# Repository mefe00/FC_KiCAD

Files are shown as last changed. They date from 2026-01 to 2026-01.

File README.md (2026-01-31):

# FC_KiCAD
Projede STM32F405RGT6 MCU, ICM-42688-P IMU, BMP388 basınç sensörü ve istenirse harici takılabilmesi için SPI çıkışı ve I2C çıkışı mevcuttur. Projenin yazılımı github hesabım üzerinde mevcuttur ve geliştirilme aşamasındadır.

fc
cfff

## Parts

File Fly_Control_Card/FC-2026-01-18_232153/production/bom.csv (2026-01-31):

Designator | Footprint | Quantity | Value | LCSC Part #
C13, C21, C25, C28, C29 | 0603 | 5 | 100nF
C14, C16 | 0603 | 2 | 4.7uF/50V
C15 | 0603 | 1 | 0.1uF/50V
C17 | 0603 | 1 | 82pF/16V
C18, C19 | 0603 | 2 | 22uF/16V
C2, C3, C37, C4, C5, C9 | 0402 | 6 | 100nF
C20 | 0603 | 1 | 0.1uF/16V
C22, C24, C26, C27 | 0402 | 4 | 1uF
C23 | 0603 | 1 | 10nF/16V
C30, C31 | 0402 | 2 | 20pF
C40, C41, C7 | 0402 | 3 | 2.2uF
C6, C8 | 0402 | 2 | 0.1uF
D2 | D_SMA | 1 | SMAJ33A
D3 | D_SMC | 1 | D
D4 | 0603 | 1 | RED_LED
D5 | 0603 | 1 | BLUE_LED
D6 | 0603 | 1 | GREEN_LED
J1 | JST_SH_SM05B-SRSS-TB_1x05-1MP_P1.00mm_Horizontal | 1 | Conn_01x05_Socket
J2, J4, J5 | JST_SH_SM04B-SRSS-TB_1x04-1MP_P1.00mm_Horizontal | 3 | Conn_01x04_Socket
J6 | SolderWire-0.1sqmm_1x02_P3.6mm_D0.4mm_OD1mm | 1 | Conn_01x02_Pin
J7 | USB_C_Receptacle_GCT_USB4105-xx-A_16P_TopMnt_Horizontal | 1 | USB_C_Receptacle_USB2.0_16P
J8 | JST_SH_SM08B-SRSS-TB_1x08-1MP_P1.00mm_Horizontal | 1 | Conn_01x08_Socket
J9 | JST_SH_SM06B-SRSS-TB_1x06-1MP_P1.00mm_Horizontal | 1 | Conn_01x06_Socket
L1 | L_APV_ANR4026 | 1 | 10uH
R1, R2 | 0402 | 2 | 5.1k
R10 | 0603 | 1 | 3.16k
R11, R4 | 0402 | 2 | 330R
R12 | 0603 | 1 | 100k
R13 | 0402 | 1 | 1k
R14, R8 | 0402 | 2 | 4.7k
R15, R7 | 0402 | 2 | 10k
R16 | 0805 | 1 | 30k (28.18k)
R17 | 0805 | 1 | 10k
R18 | 0402 | 1 | 0
R19 | 0805 | 1 | 1k
R3 | 0402 | 1 | 100k
R5, R6 | 0402 | 2 | 22R
R9 | 0603 | 1 | 10k
SW1 | SW_Push_1P1T_NO_CK_KMR2 | 1 | SW_Push
U1 | LQFP-64_10x10mm_P0.5mm | 1 | STM32F405RGTx
U2 | SOT-23-6 | 1 | USBLC6-2SC6
U3 | SOT-23-5 | 1 | LP5907MFX-3.3
U5 | PQFN50P300X250X97-14N | 1 | ICM-42688-P
U6 | PQFN50P200X200X80-10N | 1 | BMP388
U7 | SOIC127P600X175-9N | 1 | RT8279GSP
U9 | SOT-23-5 | 1 | AP2112K-3.3
Y1 | Crystal_SMD_5032-2Pin_5.0x3.2mm | 1 | 8MHz

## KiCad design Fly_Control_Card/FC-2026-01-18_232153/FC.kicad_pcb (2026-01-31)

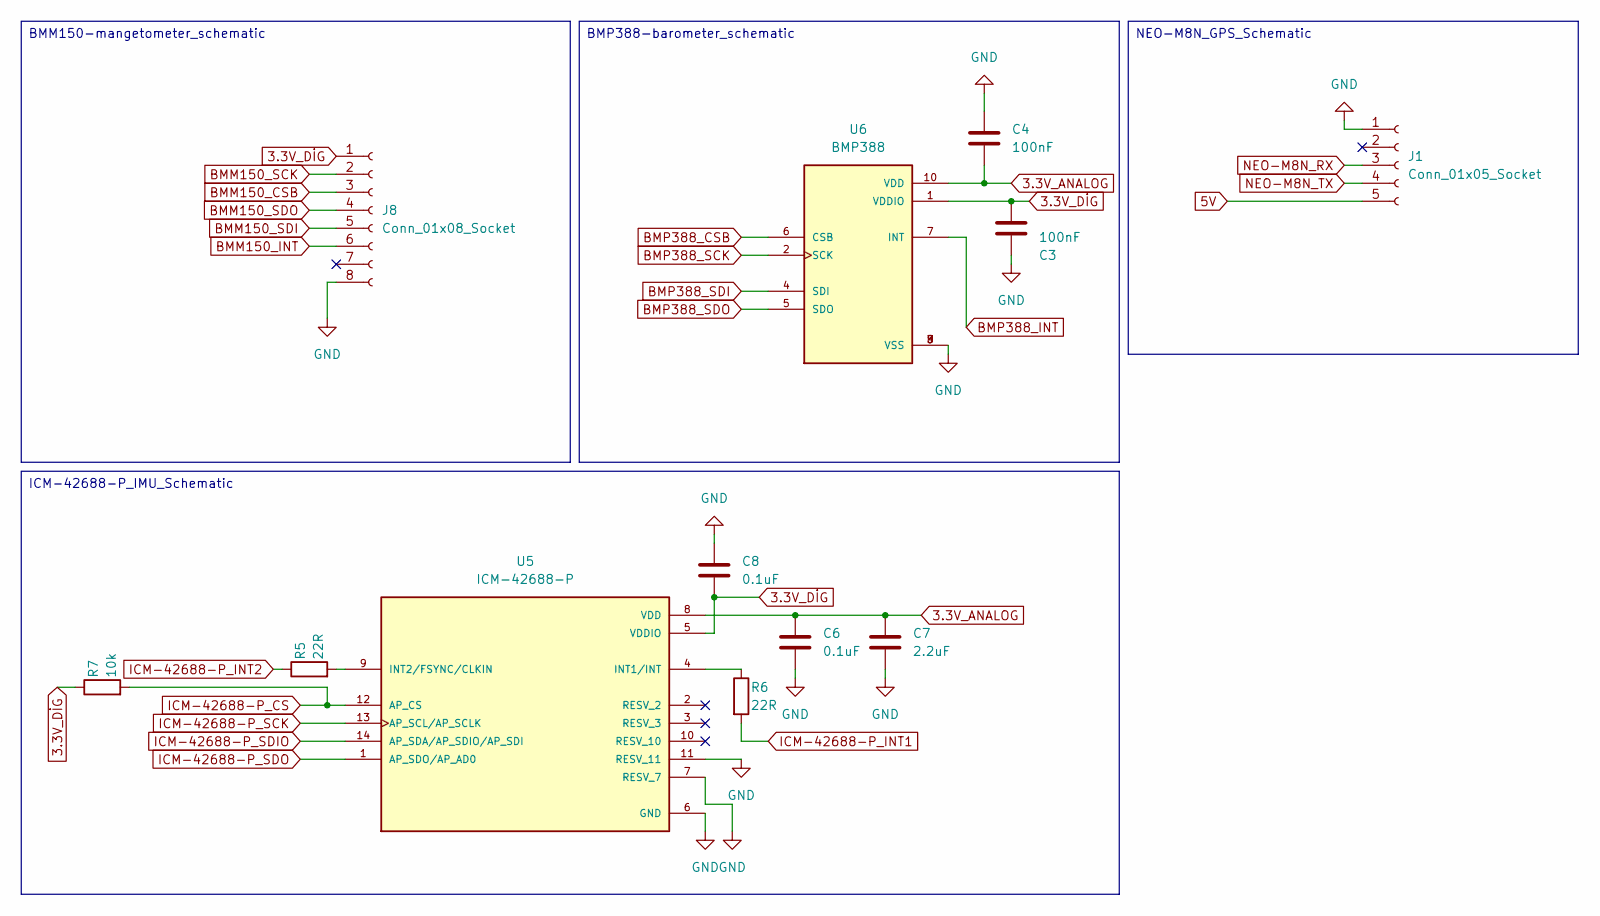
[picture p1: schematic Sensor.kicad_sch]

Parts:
C3, C4: 100nF; C_0402_1005Metric
C6, C8: 0.1uF; C_0402_1005Metric
C7: 2.2uF; C_0402_1005Metric
J1: Conn_01x05_Socket; JST_SH_SM05B-SRSS-TB_1x05-1MP_P1.00mm_Horizontal
J8: Conn_01x08_Socket; JST_SH_SM08B-SRSS-TB_1x08-1MP_P1.00mm_Horizontal
R5, R6: 22R; R_0402_1005Metric
R7: 10k; R_0402_1005Metric
U5: ICM-42688-P; PQFN50P300X250X97-14N; PARTREV 1.2
U6: BMP388; PQFN50P200X200X80-10N; PARTREV 1.1

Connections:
3.3V_ANALOG: C4.2, C6.1, C7.1, U5.8 (VDD), U6.10 (VDD); also elsewhere on the board
3.3V_DİG: C3.1, C8.2, J8.1, R7.1, U5.5 (VDDIO), U6.1 (VDDIO); also elsewhere on the board
5V: J1.5; also elsewhere on the board
BMM150_CSB: J8.3; also elsewhere on the board
BMM150_INT: J8.6; also elsewhere on the board
BMM150_SCK: J8.2; also elsewhere on the board
BMM150_SDI: J8.5; also elsewhere on the board
BMM150_SDO: J8.4; also elsewhere on the board
BMP388_CSB: U6.6 (CSB); also elsewhere on the board
BMP388_INT: U6.7 (INT); also elsewhere on the board
BMP388_SCK: U6.2 (SCK); also elsewhere on the board
BMP388_SDI: U6.4 (SDI); also elsewhere on the board
BMP388_SDO: U6.5 (SDO); also elsewhere on the board
GND: C3.2, C4.1, C6.2, C7.2, C8.1, J1.1, J8.8, U5.6 (GND), U5.7 (RESV_7), U5.11 (RESV_11), U6.3 (VSS), U6.8 (VSS), U6.9 (VSS); also elsewhere on the board
ICM-42688-P_CS: R7.2, U5.12 (AP_CS); also elsewhere on the board
ICM-42688-P_INT1: R6.2; also elsewhere on the board
ICM-42688-P_INT2: R5.1; also elsewhere on the board
ICM-42688-P_SCK: U5.13 (AP_SCL/AP_SCLK); also elsewhere on the board
ICM-42688-P_SDIO: U5.14 (AP_SDA/AP_SDIO/AP_SDI); also elsewhere on the board
ICM-42688-P_SDO: U5.1 (AP_SDO/AP_AD0); also elsewhere on the board
NEO-M8N_RX: J1.3; also elsewhere on the board
NEO-M8N_TX: J1.4; also elsewhere on the board
unnamed: R6.1, U5.4 (INT1/INT)
unnamed: R5.2, U5.9 (INT2/FSYNC/CLKIN)

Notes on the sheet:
BMP388-barometer_schematic
NEO-M8N_GPS_Schematic
BMM150-mangetometer_schematic
ICM-42688-P_IMU_Schematic

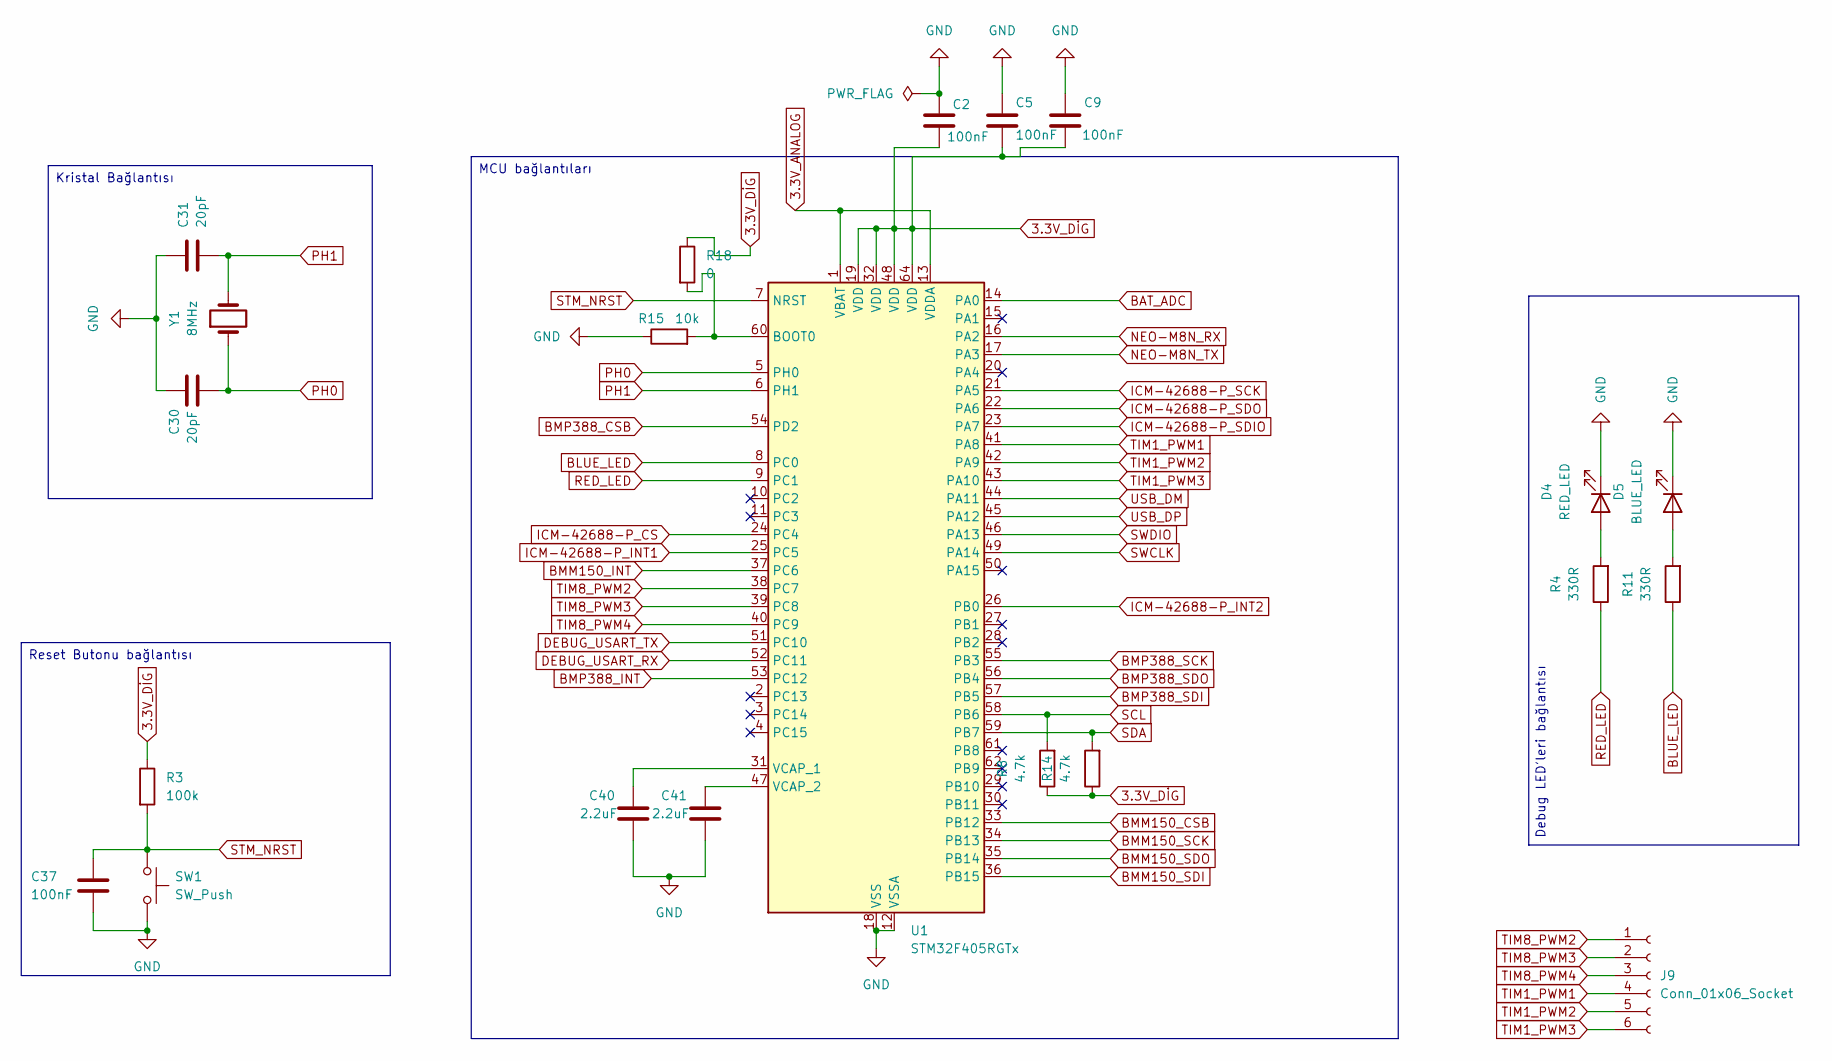
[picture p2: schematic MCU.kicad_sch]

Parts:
C2, C5, C9, C37: 100nF; C_0402_1005Metric
C30, C31: 20pF; C_0402_1005Metric
C40, C41: 2.2uF; C_0402_1005Metric
D4: RED_LED; LED_0603_1608Metric
D5: BLUE_LED; LED_0603_1608Metric
J9: Conn_01x06_Socket; JST_SH_SM06B-SRSS-TB_1x06-1MP_P1.00mm_Horizontal
R3: 100k; R_0402_1005Metric
R4, R11: 330R; R_0402_1005Metric
R8, R14: 4.7k; R_0402_1005Metric
R15: 10k; R_0402_1005Metric
R18: 0; R_0402_1005Metric
SW1: SW_Push; SW_Push_1P1T_NO_CK_KMR2
U1: STM32F405RGTx; LQFP-64_10x10mm_P0.5mm
Y1: 8MHz; Crystal_SMD_5032-2Pin_5.0x3.2mm

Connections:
3.3V_ANALOG: U1.1 (VBAT), U1.13 (VDDA); also elsewhere on the board
3.3V_DİG: C2.2, C5.2, C9.2, R3.1, R8.1, R14.1, R18.1, U1.19 (VDD), U1.32 (VDD), U1.48 (VDD), U1.64 (VDD); also elsewhere on the board
BAT_ADC: U1.14 (PA0); also elsewhere on the board
BLUE_LED: R11.1, U1.8 (PC0)
BMM150_CSB: U1.33 (PB12); also elsewhere on the board
BMM150_INT: U1.37 (PC6); also elsewhere on the board
BMM150_SCK: U1.34 (PB13); also elsewhere on the board
BMM150_SDI: U1.36 (PB15); also elsewhere on the board
BMM150_SDO: U1.35 (PB14); also elsewhere on the board
BMP388_CSB: U1.54 (PD2); also elsewhere on the board
BMP388_INT: U1.53 (PC12); also elsewhere on the board
BMP388_SCK: U1.55 (PB3); also elsewhere on the board
BMP388_SDI: U1.57 (PB5); also elsewhere on the board
BMP388_SDO: U1.56 (PB4); also elsewhere on the board
DEBUG_USART_RX: U1.52 (PC11); also elsewhere on the board
DEBUG_USART_TX: U1.51 (PC10); also elsewhere on the board
GND: C2.1, C5.1, C9.1, C30.1, C31.1, C37.2, C40.2, C41.2, D4.1 (K), D5.1 (K), R15.1, SW1.2, U1.12 (VSSA), U1.18 (VSS), U1.63 (VSS); also elsewhere on the board
ICM-42688-P_CS: U1.24 (PC4); also elsewhere on the board
ICM-42688-P_INT1: U1.25 (PC5); also elsewhere on the board
ICM-42688-P_INT2: U1.26 (PB0); also elsewhere on the board
ICM-42688-P_SCK: U1.21 (PA5); also elsewhere on the board
ICM-42688-P_SDIO: U1.23 (PA7); also elsewhere on the board
ICM-42688-P_SDO: U1.22 (PA6); also elsewhere on the board
NEO-M8N_RX: U1.16 (PA2); also elsewhere on the board
NEO-M8N_TX: U1.17 (PA3); also elsewhere on the board
unnamed: D4.2 (A), R4.2
unnamed: D5.2 (A), R11.2
unnamed: R15.2, R18.2, U1.60 (BOOT0)
unnamed: C40.1, U1.31 (VCAP_1)
unnamed: C41.1, U1.47 (VCAP_2)
PH0: C30.2, U1.5 (PH0), Y1.1
PH1: C31.2, U1.6 (PH1), Y1.2
RED_LED: R4.1, U1.9 (PC1)
SCL: R8.2, U1.58 (PB6); also elsewhere on the board
SDA: R14.2, U1.59 (PB7); also elsewhere on the board
STM_NRST: C37.1, R3.2, SW1.1, U1.7 (NRST)
SWCLK: U1.49 (PA14); also elsewhere on the board
SWDIO: U1.46 (PA13); also elsewhere on the board
TIM1_PWM1: J9.4, U1.41 (PA8)
TIM1_PWM2: J9.5, U1.42 (PA9)
TIM1_PWM3: J9.6, U1.43 (PA10)
TIM8_PWM2: J9.1, U1.38 (PC7)
TIM8_PWM3: J9.2, U1.39 (PC8)
TIM8_PWM4: J9.3, U1.40 (PC9)
USB_DM: U1.44 (PA11); also elsewhere on the board
USB_DP: U1.45 (PA12); also elsewhere on the board

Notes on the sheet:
Kristal Bağlantısı
Reset Butonu bağlantısı
Debug LED'leri bağlantısı
MCU bağlantıları

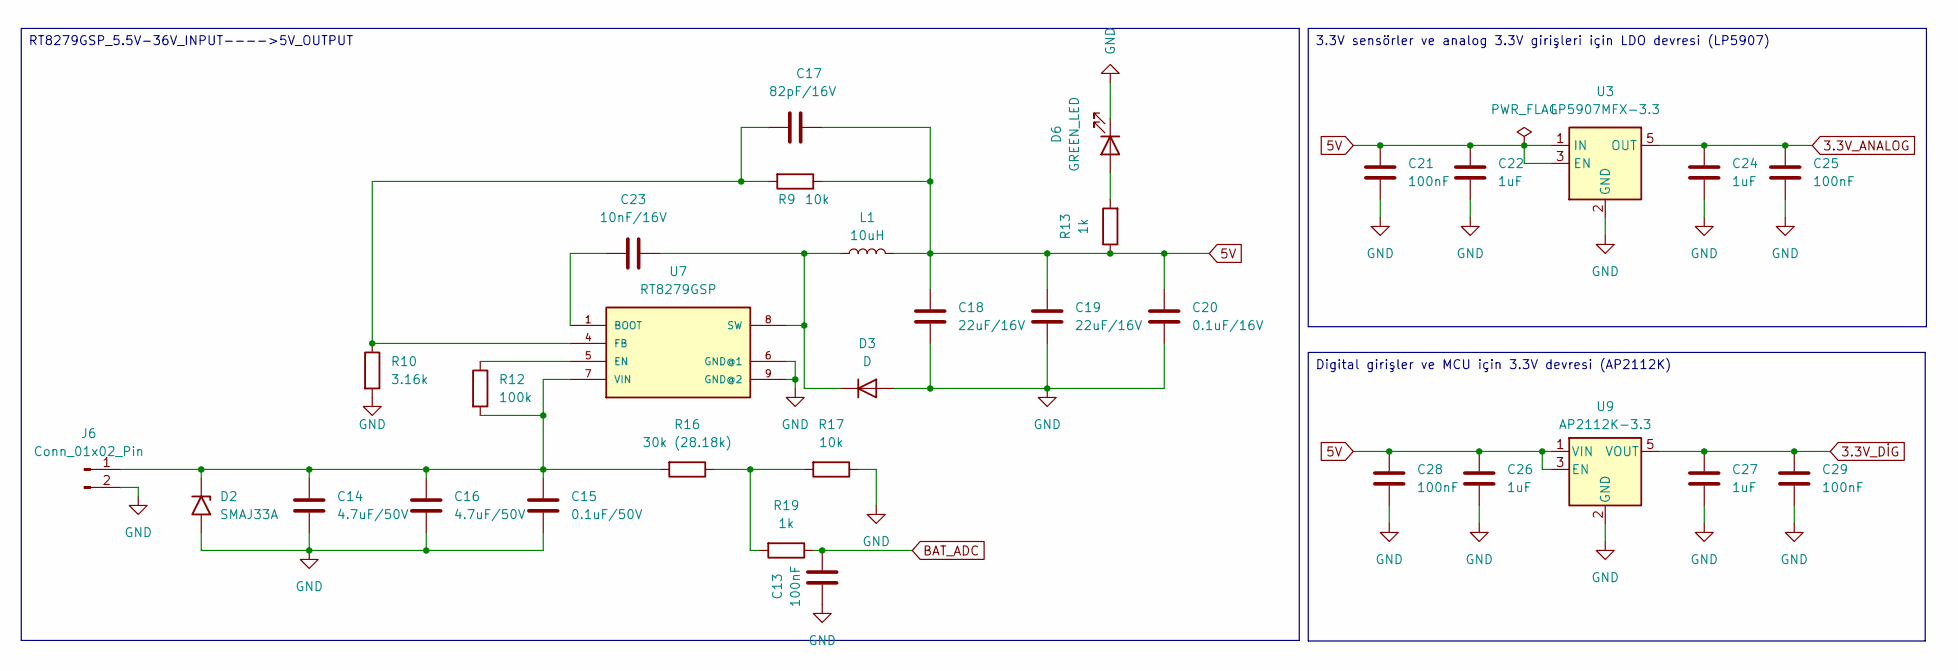
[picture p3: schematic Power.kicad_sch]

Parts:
C13, C21, C25, C28, C29: 100nF; C_0603_1608Metric
C14, C16: 4.7uF/50V; C_0603_1608Metric
C15: 0.1uF/50V; C_0603_1608Metric
C17: 82pF/16V; C_0603_1608Metric
C18, C19: 22uF/16V; C_0603_1608Metric
C20: 0.1uF/16V; C_0603_1608Metric
C22, C24, C26, C27: 1uF; C_0402_1005Metric
C23: 10nF/16V; C_0603_1608Metric
D2: SMAJ33A; D_SMA
D3: D; D_SMC
D6: GREEN_LED; LED_0603_1608Metric
J6: Conn_01x02_Pin; SolderWire-0.1sqmm_1x02_P3.6mm_D0.4mm_OD1mm
L1: 10uH; L_APV_ANR4026
R9: 10k; R_0603_1608Metric
R10: 3.16k; R_0603_1608Metric
R12: 100k; R_0603_1608Metric
R13: 1k; R_0402_1005Metric
R16: 30k (28.18k); R_0805_2012Metric
R17: 10k; R_0805_2012Metric
R19: 1k; R_0805_2012Metric
U3: LP5907MFX-3.3; SOT-23-5
U7: RT8279GSP; SOIC127P600X175-9N
U9: AP2112K-3.3; SOT-23-5

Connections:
3.3V_ANALOG: C24.1, C25.1, U3.5 (OUT); also elsewhere on the board
3.3V_DİG: C27.1, C29.1, U9.5 (VOUT); also elsewhere on the board
5V: C17.1, C18.1, C19.1, C20.1, C21.1, C22.1, C26.1, C28.1, L1.2, R9.1, R13.1, U3.1 (IN), U3.3 (EN), U9.1 (VIN), U9.3 (EN); also elsewhere on the board
BAT_ADC: C13.2, R19.1; also elsewhere on the board
GND: C13.1, C14.2, C15.2, C16.2, C18.2, C19.2, C20.2, C21.2, C22.2, C24.2, C25.2, C26.2, C27.2, C28.2, C29.2, D2.2 (A2), D3.2 (A), D6.1 (K), J6.2, R10.2, R17.1, U3.2 (GND), U7.6 (GND@1), U7.9 (GND@2), U9.2 (GND); also elsewhere on the board
unnamed: C14.1, C15.1, C16.1, D2.1 (A1), J6.1, R12.2, R16.2, U7.7 (VIN)
unnamed: C23.2, D3.1 (K), L1.1, U7.8 (SW)
unnamed: D6.2 (A), R13.2
unnamed: R16.1, R17.2, R19.2
unnamed: C23.1, U7.1 (BOOT)
unnamed: R12.1, U7.5 (EN)
unnamed: C17.2, R9.2, R10.1, U7.4 (FB)

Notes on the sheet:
3.3V sensörler ve analog 3.3V girişleri için LDO devresi (LP5907)
RT8279GSP_5.5V-36V_INPUT---->5V_OUTPUT
Digital girişler ve MCU için 3.3V devresi (AP2112K)

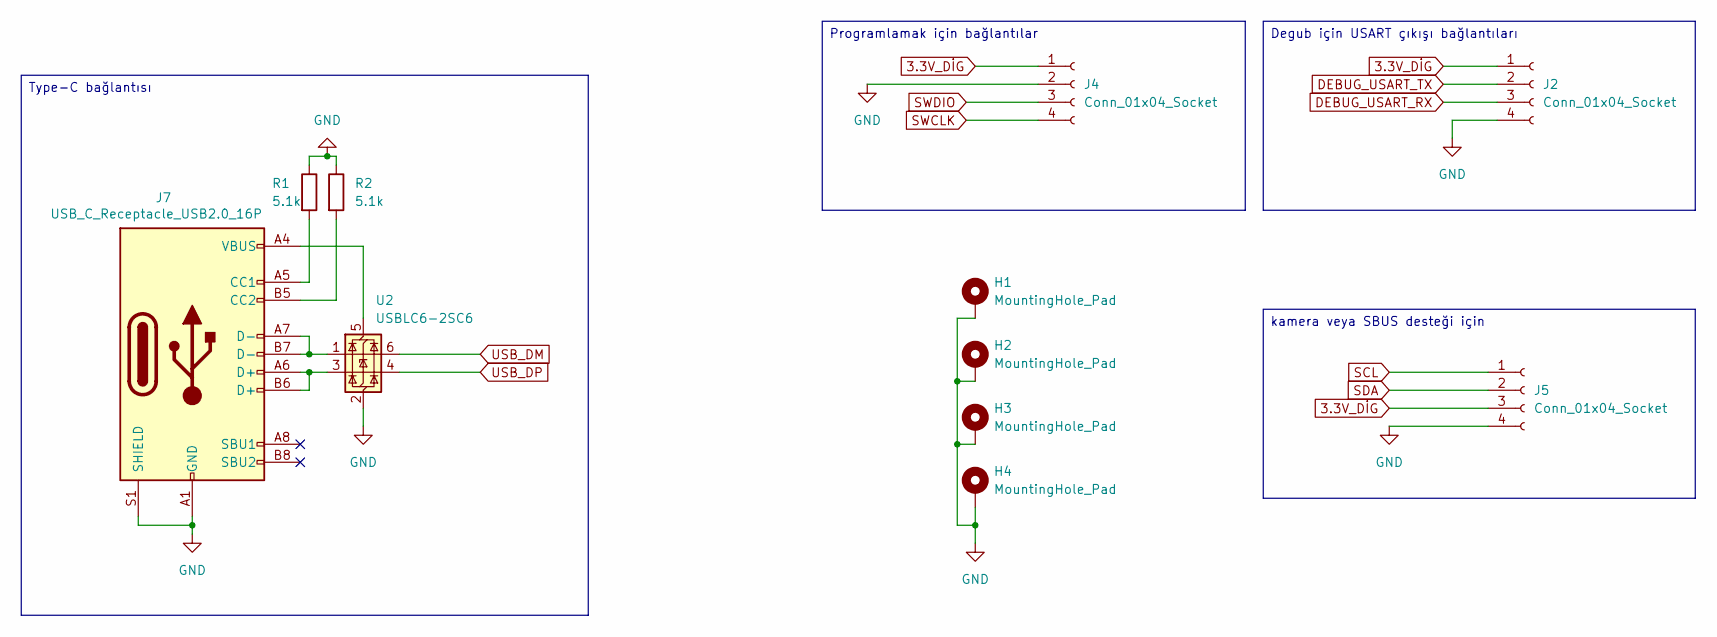
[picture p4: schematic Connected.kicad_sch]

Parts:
H1, H2, H3, H4: MountingHole_Pad; MountingHole_3.2mm_M3_Pad_Via
J2, J4, J5: Conn_01x04_Socket; JST_SH_SM04B-SRSS-TB_1x04-1MP_P1.00mm_Horizontal
J7: USB_C_Receptacle_USB2.0_16P; USB_C_Receptacle_GCT_USB4105-xx-A_16P_TopMnt_Horizontal
R1, R2: 5.1k; R_0402_1005Metric
U2: USBLC6-2SC6; SOT-23-6

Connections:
3.3V_DİG: J2.1, J4.1, J5.3; also elsewhere on the board
DEBUG_USART_RX: J2.3; also elsewhere on the board
DEBUG_USART_TX: J2.2; also elsewhere on the board
GND: H1.1, H2.1, H3.1, H4.1, J2.4, J4.2, J5.4, J7.A1 (GND), J7.A12 (GND), J7.B1 (GND), J7.B12 (GND), J7.S1 (SHIELD), R1.1, R2.1, U2.2 (GND); also elsewhere on the board
unnamed: J7.A5 (CC1), R1.2
unnamed: J7.B5 (CC2), R2.2
unnamed: J7.A6 (D+), J7.B6 (D+), U2.3 (I/O2)
unnamed: J7.A7 (D-), J7.B7 (D-), U2.1 (I/O1)
unnamed: J7.A4 (VBUS), J7.A9 (VBUS), J7.B4 (VBUS), J7.B9 (VBUS), U2.5 (VBUS)
SCL: J5.1; also elsewhere on the board
SDA: J5.2; also elsewhere on the board
SWCLK: J4.4; also elsewhere on the board
SWDIO: J4.3; also elsewhere on the board
USB_DM: U2.6 (I/O1); also elsewhere on the board
USB_DP: U2.4 (I/O2); also elsewhere on the board

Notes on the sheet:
Degub için USART çıkışı bağlantıları
kamera veya SBUS desteği için
Programlamak için bağlantılar
Type-C bağlantısı

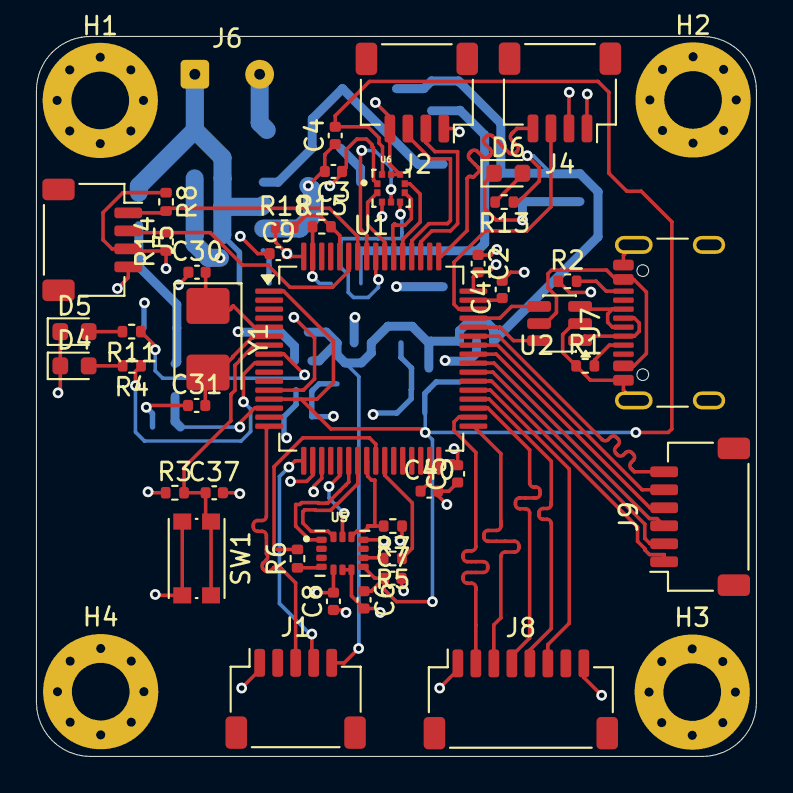
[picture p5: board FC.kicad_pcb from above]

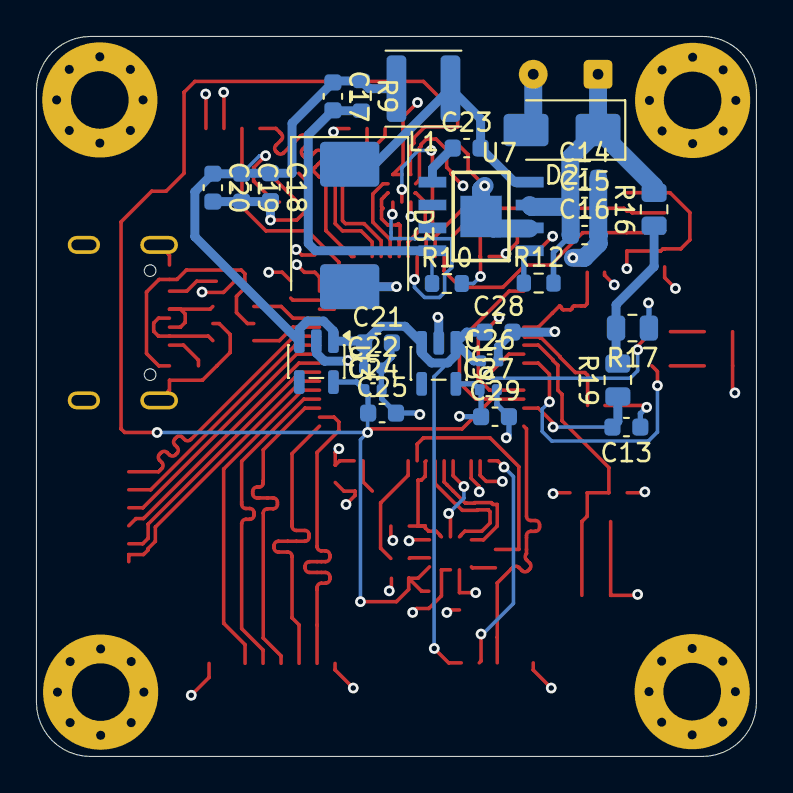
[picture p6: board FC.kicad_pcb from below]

Board: 4 copper layers, 40.0 x 40.0 mm, 76 parts (29 on the bottom side), 61 nets.
